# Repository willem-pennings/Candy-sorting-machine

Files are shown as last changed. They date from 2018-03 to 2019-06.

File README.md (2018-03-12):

# Candy sorting machine
This machine sorts M&Ms or Skittles by colour using a TCS34725 colour sensor. Two stepper motors actuate the moving parts (these are the "feed wheel" and the "carousel") while a modified micro servo motor mixes the pieces that enter the system.

# 3D models
The 3D models are provided in the STL format and are ready for 3D printing. The parts that I use are made of nylon (also referred to as PA-12 sometimes) and were printed in an SLS process.

# Source code
The machine uses two separate Arduino devices. One controls the sorting process (including sensors, actuators and logic) whereas the other only controls the RGB LEDs. It receives commands from the aforementioned (primary) Arduino device. There are three Arduino sketches available for download:

- The `sortingmachine` is the main sketch and contains all code necessary to run the sorting process.
- The `sortingmachine_calibration` sketch is much like the `sortingmachine` sketch, but is slightly modified such that the machine can be quickly calibrated using pre-sorted M&Ms or Skittles. For example, the carousel motor is disabled in this sketch and serial output is condensed for easy data exporting.
- The `sortingmachine_lighting` sketch controls the RGB leds. It communicates with the primary Arduino device through I2C (TWI) and should be connected accordingly. Part of this code was written by Bill Earl.

# Note
All files are provided as-is. I welcome any questions, but some effort will be needed to fully comprehend the code structure. Additionally, I appreciate it when others send in their derivative works. You can contact me through my website, https://willemm.nl.

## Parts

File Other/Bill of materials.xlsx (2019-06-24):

Parts related to the sorting mechanism and electronics of the machine
Quantity | Part name | Available at
1 | 3D-printed parts | https://github.com/willem-pennings/Candy-sorting-machine
2 | Arduino Nano | Various
2 | Stepper motor ROB-09238 | https://www.sparkfun.com/products/9238
2 | EasyDriver ROB-12779 | https://www.sparkfun.com/products/12779
1 | Roller lever microswitch ROB-13119 | https://www.sparkfun.com/products/13119
6 | Bowls | Hema (Netherlands)
1 | DC-DC converter (5V output) | AliExpress or locally
2 | Pushbutton with integrated LED | AliExpress or locally
1 | WS2812b LED strip (0.5 m) | AliExpress or locally
2 | Prototyping PCB (5x7 cm) | AliExpress or locally
40 | Jumper wires (length 20 cm, amount indicative) | AliExpress or locally
100 | Breadboard jumpe wires (tinned, amount indicative) | AliExpress or locally
10 | Male + female pin headers (0.1", 40 pins, amount indicative) | AliExpress or locally
1 | 22 AWG wire (power supply cabling) | AliExpress or locally
1 | DC female barrel jack | AliExpress or locally
1 | Heat shrink (various diameters) | AliExpress or locally
1 | Micro servo (9g) | AliExpress or locally
1 | TCS34725 colour sensor on breakout board | https://www.adafruit.com/product/1334
4 | M4x30 bolts and nuts | Hardware store
4 | M3x12 bolts and nuts | Hardware store
4 | M4 washer | Hardware store
4 | M3 washer | Hardware store
Parts related to the housing of the machine
1 | Lasercut MDF parts | Design your own
1 | Copper tube (15 mm diameter, 1 meter length) | Hardware store
1 | Threaded rod M3 (2 meter length) | Hardware store
10 | Cap nuts M3 | Hardware store
1 | White spray paint | Hardware store
1 | Primer (paint) | Hardware store
1 | Sandpaper (various roughnesses) | Hardware store
1 | Wood glue | Hardware store
1 | PVC tubing (diameter 250 mm, wall thickness 10 mm) | Hardware store (maybe)

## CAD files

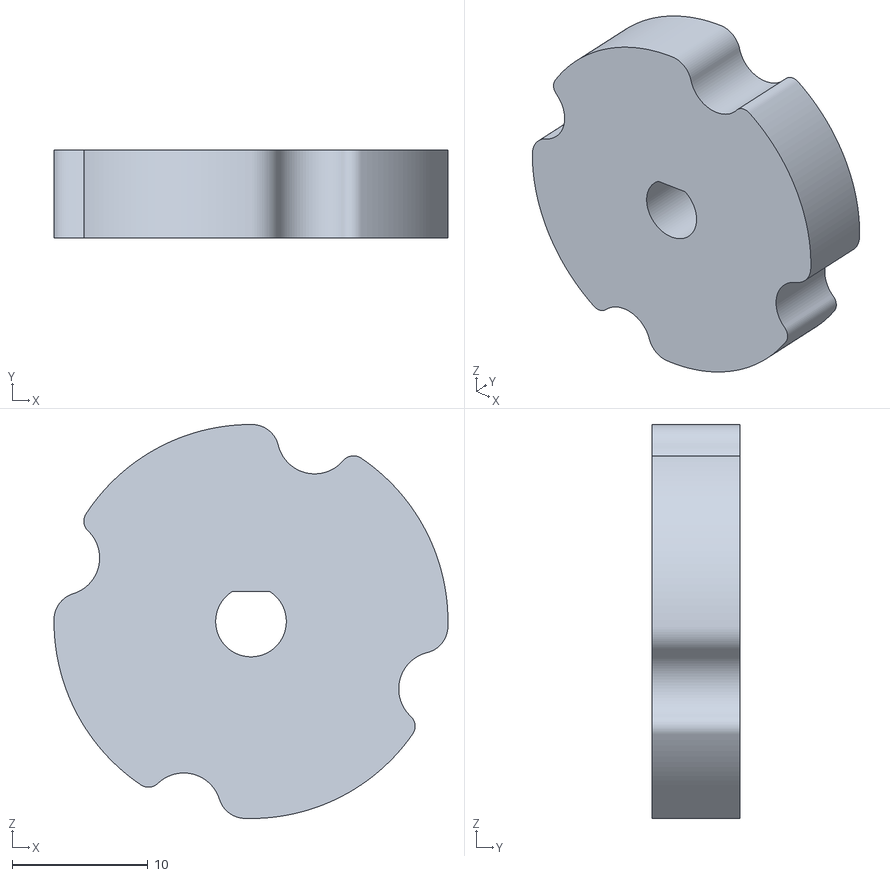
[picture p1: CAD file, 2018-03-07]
3D models/wheelsyncer.stl
29.0 x 6.50 x 29.0

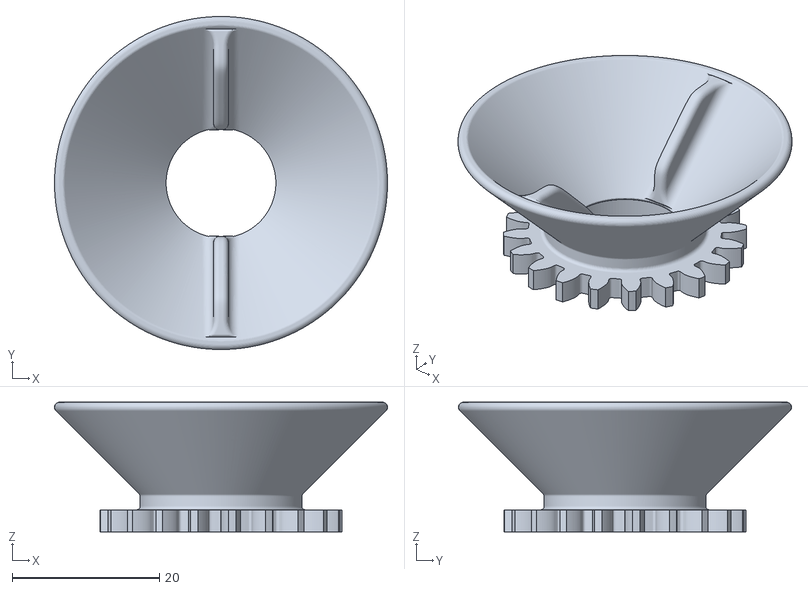
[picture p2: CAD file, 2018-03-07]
3D models/stirfunnel.stl
45.3 x 45.3 x 17.6

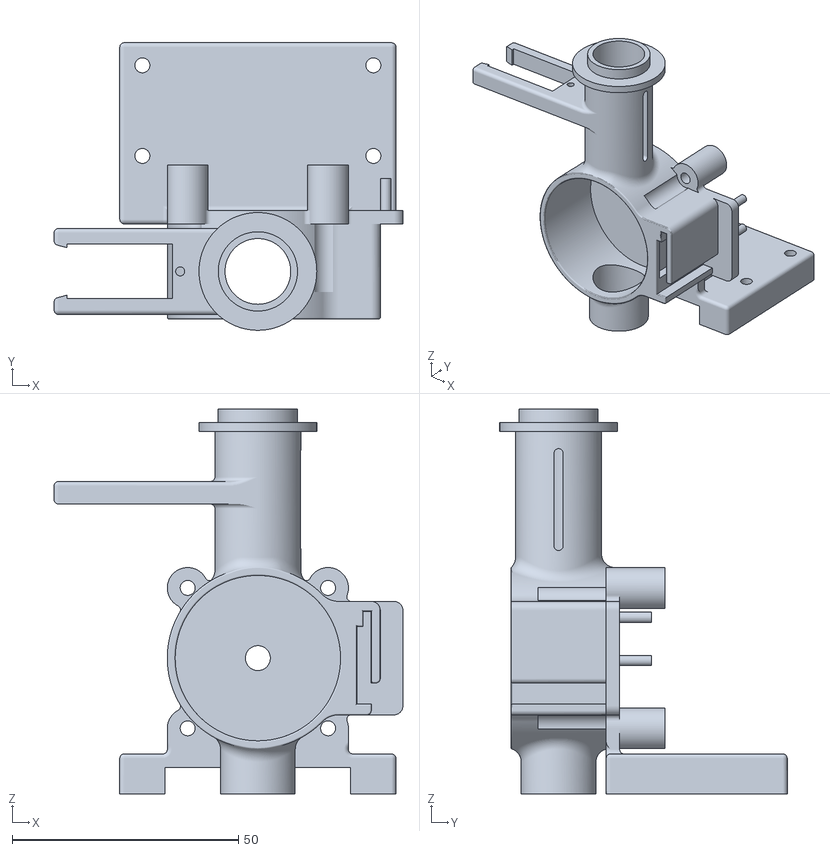
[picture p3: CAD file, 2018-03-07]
3D models/wheelhousing.stl
77.0 x 63.5 x 85.0

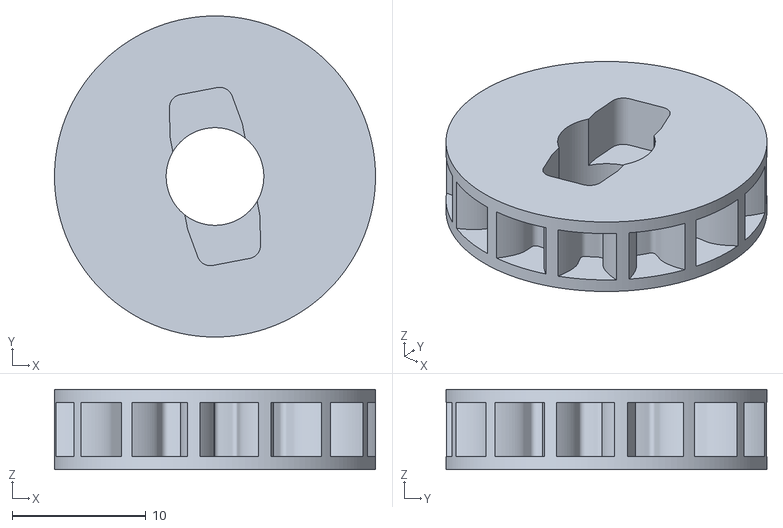
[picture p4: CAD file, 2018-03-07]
3D models/servogear.stl
24.0 x 24.0 x 6.00

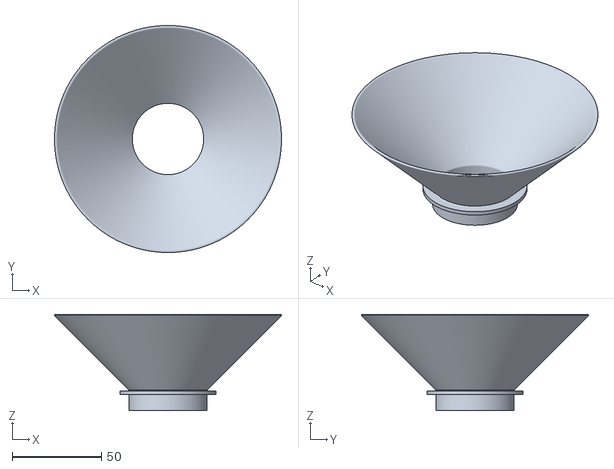
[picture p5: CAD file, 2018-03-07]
3D models/hopper.stl
127.4 x 127.4 x 53.9

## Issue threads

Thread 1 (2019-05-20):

Code problem

achrafzarrouk, 2019-05-20:
Something went wrong during  compilation
It just crashes on stepper.stop

willem-pennings, 2019-06-24:
Hi, have you downloaded all required libraries and did you add them to your Arduino IDE?

Closed 2019-08-10.

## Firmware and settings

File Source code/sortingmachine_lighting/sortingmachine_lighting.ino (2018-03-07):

#include <Wire.h>
#include <Adafruit_NeoPixel.h>
#include <EasyTransferI2C.h>
#include <Servo.h>

#define NUM_LEDS1   32 // The amount of LEDs in the color ring
#define NUM_LEDS2   6 // The amount of LEDs for the spot lights
#define LED_PIN1    10 // Digital pin for the WS2812B circle
#define LED_PIN2    11 // Digital pin for the WS2812B spot lights
#define SERVO1      3 // Digital pin for the servo
#define BRIGHTNESS1 80 // LED ring brightness
#define BRIGHTNESS2 80 // LED spots brightness

int servoSpeed = 100; // Rotational speed of the servo

typedef enum {mm_red, mm_green, mm_blue, mm_yellow, mm_orange, mm_brown, sk_red, sk_green, sk_yellow, sk_orange, sk_purple, unknown} ItemColor;
typedef enum {standby, loaditem, analyzecolor, determinecolor, setreleasepos, releaseitem, reverse} State;
typedef enum {mms, skittles} CandyType;

// Initialize servo
Servo mixservo;

// Variable sync initialization
EasyTransferI2C ET;

struct SYNC_CONTAINER {
  ItemColor nextcolor;
  ItemColor prevcolor;
  State state;
  CandyType candytype;
};

SYNC_CONTAINER sync;

State state = standby;

ItemColor nextcolor;
ItemColor prevcolor;

CandyType candytype = mms;

const int ringDelay = 9;

unsigned long lastTime = 0;
const int delayTime = 500;

unsigned int currentLed = 5;

uint32_t ringColor;

#include "lighting.h"

void setup() {
  Wire.begin(8);
  ET.begin(details(sync), &Wire);
  Wire.onReceive(receive);
  Serial.begin(115200);
  
  // Initialize all the pixelStrips and set the ring brightness
  ring.begin();
  ring.setBrightness(BRIGHTNESS1);
  spots.begin();
  spots.setBrightness(BRIGHTNESS2);
  
  Serial.println(F("INFO\t\tLighting Arduino was initialized and I2C communication was succesfully started!"));

  // Send all-good signal to master
  Wire.beginTransmission(7);
  Wire.write(millis());
  Wire.endTransmission();
}

void loop() {
  if(ET.receiveData()) {
    state = sync.state;
    prevcolor = sync.prevcolor;
    nextcolor = sync.nextcolor;
    Serial.println(F("INFO\t\tReceived & updated sync variables from device 1."));
    
    switch(state) {
    case standby:
      if(sync.candytype != candytype) {
        Serial.println(F("INFO\t\tCandy type has changed! Providing feedback through the spot lights."));
        if(sync.candytype == mms) {
          for(int i = 0; i < NUM_LEDS2; i++) {
            spots.setPixelColor(i, blue);
          }
          spots.show();
          delay(1000);
          for(int i = 0; i < NUM_LEDS2; i++) {
            spots.setPixelColor(i, black);
          }
          spots.show();
        } else if(sync.candytype == skittles) {
          for(int i = 0; i < NUM_LEDS2; i++) {
            spots.setPixelColor(i, red);
          }
          spots.show();
          delay(1000);
          for(int i = 0; i < NUM_LEDS2; i++) {
            spots.setPixelColor(i, black);
          }
          spots.show();
        }
        candytype = sync.candytype;
      }

      // Initialize a rainbow pattern on the spot lights
      spots.ActivePattern = RAINBOW_CYCLE;
      spots.TotalSteps = 255;
      spots.Interval = min(10, spots.Interval);
      spots.RainbowCycle(ringDelay);

      // Enable a rainbow effect on the LED ring
      ring.ActivePattern = RAINBOW_CYCLE;
      ring.TotalSteps = 255;
      ring.Interval = min(10, ring.Interval);
      ring.RainbowCycle(ringDelay);
      Serial.println(F("INFO\t\tReceived state is standby. Rainbow patterns were activated."));

      mixservo.detach();
      
      break;
    case determinecolor:
      ring.ActivePattern = NONE;
      spots.ActivePattern = NONE;
      Serial.println(F("INFO\t\tCurrently not in standby mode. Setting new ring color & updating spots."));

      // Turn off all spots before setting a new color
      for(int i = 0; i < NUM_LEDS2; i++) {
        spots.setPixelColor(i, black);
      }
      
      switch(nextcolor) {
        case mm_red: spots.setPixelColor(4, white); ringColor = red; break;
        case mm_green: spots.setPixelColor(0, white); ringColor = green; break;
        case mm_blue: spots.setPixelColor(1, white); ringColor = blue; break;
        case mm_yellow: spots.setPixelColor(2, white); ringColor = yellow; break;
        case mm_orange: spots.setPixelColor(3, white); ringColor = orange; break;
        case mm_brown: spots.setPixelColor(5, white); ringColor = brown; break;
        case sk_red: spots.setPixelColor(5, white); ringColor = red; break;
        case sk_green: spots.setPixelColor(0, white); ringColor = green; break;
        case sk_yellow: spots.setPixelColor(1, white); ringColor = yellow; break;
        case sk_orange: spots.setPixelColor(2, white); ringColor = orange; break;
        case sk_purple: spots.setPixelColor(3, white); ringColor = purple; break;
        case unknown: spots.setPixelColor(4, white); ringColor = white; break;
      }
      
      spots.show();
      Serial.println(F("INFO\t\tSpot lights colors were set!"));

      for(int i = 0; i < NUM_LEDS1; i++) {
        ring.setPixelColor(i, ringColor);
      }
      ring.show();

      mixservo.attach(SERVO1);
      mixservo.write(servoSpeed);
      
      break;
    }
  }
  
  // Handle ring & spots lighting for standby mode (mostly in sortingprocess)
  if(ring.ActivePattern != NONE) {
    ring.Update();
    spots.Update();
  }

  /*if((millis() - lastTime > delayTime) && state == standby) {
    for(int i = 0; i < NUM_LEDS2; i++) {
      spots.setPixelColor(i, black);
    }
    spots.setPixelColor(currentLed, white);
    spots.show();
    if(currentLed == 0) {
      currentLed = 5;
    } else {
      currentLed--;
    }
    lastTime = millis();
  }*/
}

void receive(int numBytes) {}

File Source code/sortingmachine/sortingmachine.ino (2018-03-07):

/***** SUPPORT LIBRARIES *****/

#include <Wire.h>
#include <Math.h>
#include "Adafruit_TCS34725.h"
#include "Adafruit_DRV2605.h"
#include <EasyTransferI2C.h>
#include <AccelStepper.h>

#include "colorsensor.h"
#include "functions.h"
#include "sortingmachine.h"
#include "stepper.h"

/***** PIN DEFINITIONS *****/

// Microswitch input pins (internal pullup)
#define MICRO1  A0
#define MICRO2  A1

// Button input pins (internal pullup)
#define BUTTON1 A2
#define BUTTON2 A3

// EasyDriver 1 pin definitions (measurement wheel)
#define STEP1   3
#define DIR1    4
#define EN1     5

// EasyDriver 2 pin definitions (carousel motor)
#define STEP2   8
#define DIR2    9
#define EN2     10

/***** HARDWARE & COMMS *****/

// TCS34725 initialization
Adafruit_TCS34725 tcs = Adafruit_TCS34725(TCS34725_INTEGRATIONTIME_50MS, TCS34725_GAIN_4X);

// DRV2605 initialization
Adafruit_DRV2605 drv;

// Stepper initialization
AccelStepper stepper1(1,STEP1,DIR1);
AccelStepper stepper2(1,STEP2,DIR2);

// Variable sync initialization
EasyTransferI2C ET;

struct SYNC_CONTAINER {
  ItemColor nextcolor;
  ItemColor prevcolor;
  State state;
  CandyType candytype;
};

SYNC_CONTAINER sync;

/***** SETTINGS *****/

// Default candy type - 'mms' for M&Ms, 'skittles' for Skittles
CandyType candytype = mms;
// Stepper motor delay between a STEP transition [microseconds]
const unsigned int delayBetweenTransitions = 1000;
// Time between color measurements [milliseconds]
const int timeBetweenMeasurements = 25;
// The amount of measurements with an 'unknown' result before the machine goes into standby.
const int maxconsecUnknown = 30;
// The maximum amount of time allowed for the measurement wheel to load a piece of candy
const int maxLoadTime = 250;
// If true, send all debugging information over serial.
const bool debug = false;
// If true, only send important/critical information over serial.
const bool debug_important = false;

void setup() {
  // Set up serial communication at 115200 baudrate
  Serial.begin(500000);
  // Start I2C communication (address 7) and set up variable sync communication
  Wire.begin(7);
  Wire.onReceive(receive);
  ET.begin(details(sync), &Wire);
  
  if(debug){Serial.println(F("INFO\t\tM&M sorting machine by Willem Pennings"));}

  // Initialize the color sensor
  initializeTCS34725();
  // Initialize the vibrator control IC
  initializeDRV2605();
  // Initialize stepper motors
  initializeSteppers();
  // Initialize the stepper motor output pins and write default values
  initializePins();
}

void loop() {
  // The sorting process handles the different machine states and executes the bulk of the commands
  sortingProcess();

  // Check buttons and handle them if inputs are detected
  buttonHandler();

  stepper1.runSpeed();
  stepper2.run();
}

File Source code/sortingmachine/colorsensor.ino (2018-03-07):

/*
 * Color acquisition and analyzation functions
 */

/*
  TCS34725  ---------------  Arduino
  VCC       ---------------  5V
  GND       ---------------  GND
  SCL       ---------------  SCL
  SDA       ---------------  SDA
  LED       ---------------  2
*/

void measureColor(int measuredColor[]) {
  float r, g, b;
  uint16_t red, green, blue, clear;
  uint32_t sum;

  // Get raw data and store it in variables
  tcs.getRawData(&red, &green, &blue, &clear);

  // Do calculations to convert the measured values to adjusted 0-255 RGB values
  sum = clear;
  r = red; g = green; b = blue;
  r /= sum; g /= sum; b /= sum;
  r *= 256; g *= 256; b *= 256;
  measuredColor[0] = r; measuredColor[1] = g; measuredColor[2] = b;
}

void RGBtoHSV(int RGBColor[], int HSVColor[]) {
  double color[3];
  double Cmax, Cmin, delta;
  double hue, sat, val;
  double hueAngle, satPerc, valPerc;

  color[0] = RGBColor[0]; color[1] = RGBColor[1]; color[2] = RGBColor[2];

  if(debug){
    Serial.println("INFO\t\t-- Converting RGB to HSV color --");
    Serial.print("INFO\t\tInput colors are: \t");
    Serial.print(F("R: ")); Serial.print(color[0]); Serial.print(F("\t"));
    Serial.print(F("G: ")); Serial.print(color[1]); Serial.print(F("\t"));
    Serial.print(F("B: ")); Serial.println(color[2]);
  }
  
  color[0] /= 255; color[1] /= 255; color[2] /= 255;
  
  Cmax = arrayMax(color, 3);
  Cmin = arrayMin(color, 3);
  delta = Cmax - Cmin;

  if(delta == 0) {
    hue = 0;
  }
  if(Cmax == color[0]) {
    hue = (60 * fmod(((color[1] - color[2]) / delta), 6)) * 0.7083;
    if(color[1] - color[2] < 0) {
      hue += 255;
    }
  }
  if(Cmax == color[1]) {
    hue = (60 * (((color[2] - color[0]) / delta) + 2)) * 0.7083;
  }
  if(Cmax == color[2]) {
    hue = (60 * (((color[0] - color[1]) / delta) + 4)) * 0.7083;
  }

  if(Cmax == 0) {
    sat = 0;
  } else  {
    sat = (delta / Cmax) * 255;
  }
  
  val = Cmax * 255;

  HSVColor[0] = (int)hue; HSVColor[1] = (int)sat; HSVColor[2] = (int)val;
  
  if(debug){
    Serial.print(F("INFO\t\tOutput colors are: \t"));
    Serial.print(F("H: ")); Serial.print(HSVColor[0]); Serial.print(F("\t\t"));
    Serial.print(F("S: ")); Serial.print(HSVColor[1]); Serial.print(("\t\t"));
    Serial.print(F("V: ")); Serial.println(HSVColor[2]);
    hueAngle = (hue / 255) * 360; satPerc = (sat / 255) * 100; valPerc = (val / 255) * 100;
    Serial.print(F("INFO\t\tAngle-percent equiv.: \t"));
    Serial.print(F("H: ")); Serial.print(hueAngle); Serial.print(F("\t"));
    Serial.print(F("S: ")); Serial.print(satPerc); Serial.print(F("\t"));
    Serial.print(F("V: ")); Serial.println(valPerc);
    Serial.println(F("INFO\t\t-- End RGB to HSV color conversion --"));
  }
}

ItemColor determineColor(int measuredColor[]) {
  int i;
  ItemColor itemcolor = unknown;

  for(i = 0; i < 6; i++) {
    if(candytype == mms) {
      if((measuredColor[0] >= calibratedvalues[i][0][0][0]) && // H lower bound check
         (measuredColor[0] <= calibratedvalues[i][0][1][0]) && // H upper bound check
         (measuredColor[1] >= calibratedvalues[i][0][0][1]) && // S lower bound check
         (measuredColor[1] <= calibratedvalues[i][0][1][1])) { // S upper bound check
           // Set the item color when a check is succesful
           itemcolor = (ItemColor)i;
           i = 6;
      }
    }
    if(candytype == skittles) {
      if((measuredColor[0] >= calibratedvalues[i][1][0][0]) && // H lower bound check
         (measuredColor[0] <= calibratedvalues[i][1][1][0]) && // H upper bound check
         (measuredColor[1] >= calibratedvalues[i][1][0][1]) && // S lower bound check
         (measuredColor[1] <= calibratedvalues[i][1][1][1])) { // S upper bound check
           itemcolor = (ItemColor)(i + 6);
           i = 6;
      }
    }
  }

  if(debug){
    // Print the detected color
    switch(itemcolor) {
      case mm_red: Serial.println(F("INFO\t\tDetected a red M&M piece!")); break;
      case mm_green: Serial.println(F("INFO\t\tDetected a green M&M piece!")); break;
      case mm_blue: Serial.println(F("INFO\t\tDetected a blue M&M piece!")); break;
      case mm_yellow: Serial.println(F("INFO\t\tDetected a yellow M&M piece!")); break;
      case mm_orange: Serial.println(F("INFO\t\tDetected an orange M&M piece!")); break;
      case mm_brown: Serial.println(F("INFO\t\tDetected a brown M&M piece!")); break;
  
      case sk_red: Serial.println(F("INFO\t\tDetected a red Skittles piece!")); break;
      case sk_green: Serial.println(F("INFO\t\tDetected a green Skittles piece!")); break;
      case sk_yellow: Serial.println(F("INFO\t\tDetected a yellow Skittles piece!")); break;
      case sk_orange: Serial.println(F("INFO\t\tDetected an orange Skittles piece!")); break;
      case sk_purple: Serial.println(F("INFO\t\tDetected a purple Skittles piece!")); break;
  
      case unknown: Serial.println(F("WARNING\t\tFailed to get a color! Sample has been marked as unknown.")); break;
    }
  }
  return itemcolor;
}

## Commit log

2018-03-07 Public release
    [Candy dimensions.xlsx, hopper.stl, servogear.stl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]
2018-06-28 Add BOM
    [Bill of materials.xlsx]
2019-06-24 BOM update
    [Bill of materials.xlsx]
